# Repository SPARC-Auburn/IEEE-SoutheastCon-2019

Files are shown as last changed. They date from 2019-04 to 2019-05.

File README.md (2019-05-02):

# IEEE Southeastcon Hardware Competition 2019 Team - Auburn University
## Overview
The purpose of this project is to create a robot to compete in the 2019 IEEE SoutheastCon held in Huntsville, AL.  The conference is centered around sharing and demonstrating technical advancements in engineering.  We competed in the hardware competition against 40 other universities from across the southeastern US.  This project was a collaboration between Auburn's [Student Project and Research Committee (SPARC)](http://sparc.eng.auburn.edu/) and an electrical engineering senior design team.

## Game Overview
The function of the robot is to move around a square carpeted area with a side length of 244 centimeters, and pick up small objects on the field and place them into one of four colored home bases based on the color of the object. The arena is split into two zones.  Zone one features four home bases corresponding to four different colors. The robot starts in one of the four home bases.  Zone two is separated by a one-inch thick white line.  Zone two is where twelve objects are placed for the robot to pick up: eight two inch wooden cubes, and four 2.5 inch diameter pit balls. The arena features a wooden box in the middle that serves as an obstacle as well as four LED lights situated at the edge of zone two on the one-inch line.  The four home bases are placed at the four corners of the arena in zone one.  An arena was built in order to test the robot as shown in Figure 0.  This allows testing of the robot in a controlled area leading up to the competition.

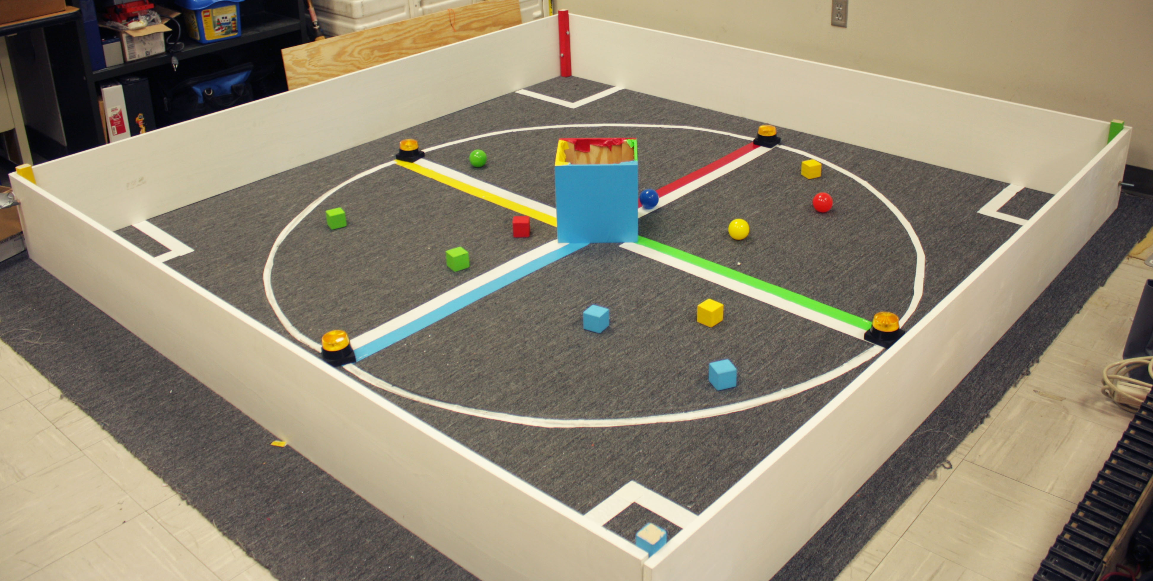
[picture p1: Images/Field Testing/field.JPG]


**Figure 0:** Field Constructed in Broun Hall room 368 

The competition had some other ways to score points such as leaving the home base, going in circles (orbits) around the center structure, and raising a flag.  There is a penalty to colliding with the flashing lights (spacetels).  Table 1 displays a summary of the scoring methods.  

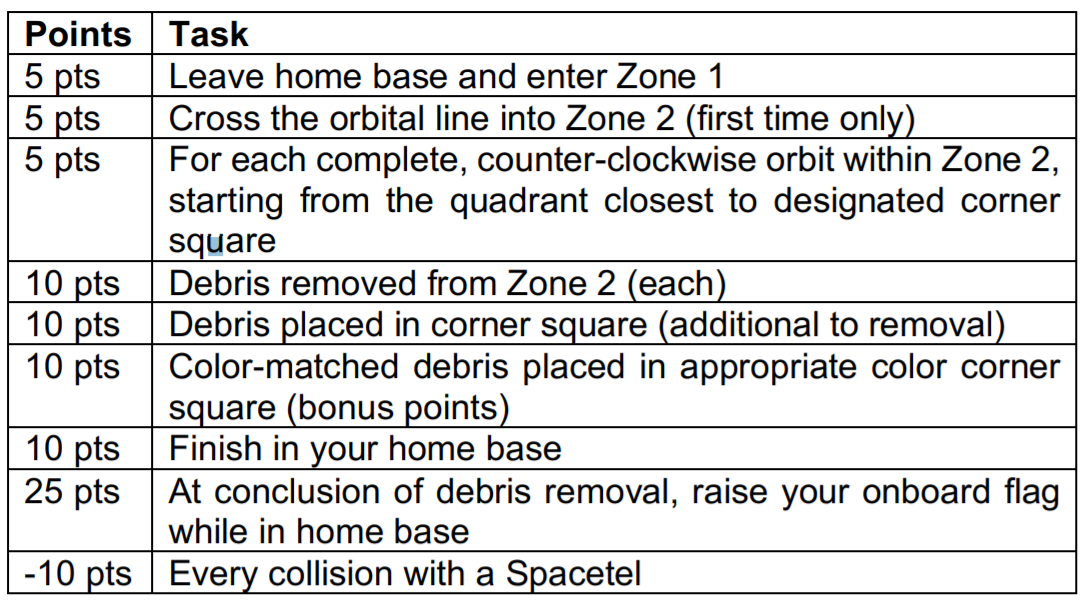
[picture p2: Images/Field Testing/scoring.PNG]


**Table 1:** Summary of scoring methods

## Robot Constraints
The robot has several constraints that limit the size of the robot, materials used in the construction that assure the safety of participants and other robots ([Competition Rules](http://sites.ieee.org/southeastcon2019/files/2019/02/2019-SoutheastCon-HW-Rules_v1_3-1.pdf)).  The robot’s width and length must be within a nine by nine-inch area and a max height of eleven inches.  The nine by nine area must include a bumper covering eighty percent of the perimeter.  The bumper must be 1.5 inches from the ground and have a minimum vertical cover of one inch, and must not have a radius of curvature less than one centimeter.  This is to prevent damage to the arena and other robots in the event of a collision.  The robot can also raise a mechanical arm, with a max length of three inches, with a flag presenting the competing school’s name.

## Our Approach
The robot utilizes two Raspberry Pi microcomputers to control the motors while using an attached camera to identify the color and shape of the objects on the field.  A LIDAR is used to localize the robot on the arena to help avoid the four lights and the wooden box in the middle of the arena.  The design of the robot is to move the objects to the appropriate home base by running over the objects, closing a small door on the front of the robot, hold them under the robot and move towards the appropriate home base of the object.  Figure 1 shows the final robot design.

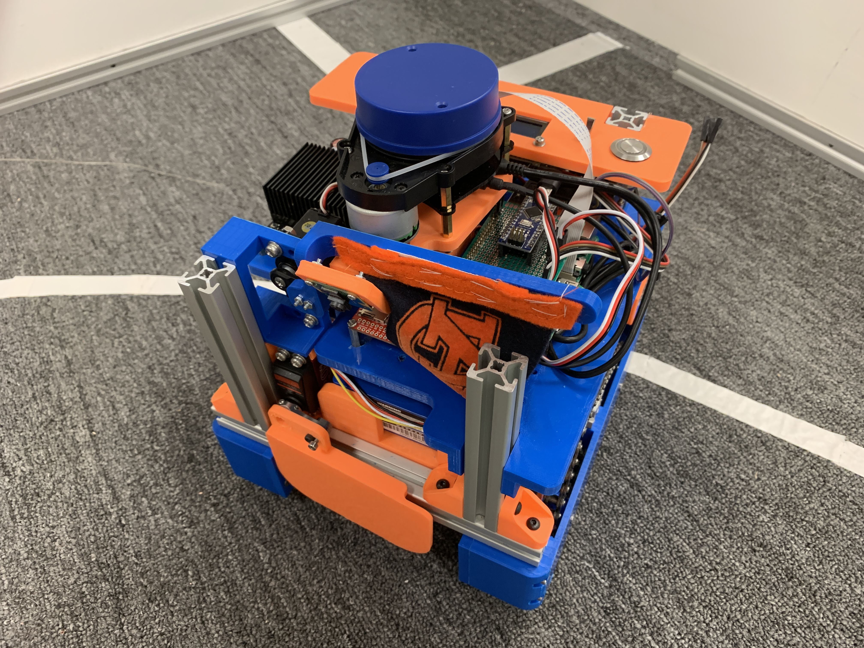
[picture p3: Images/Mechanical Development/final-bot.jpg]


**Figure 1:** Final robot design

## Technical Documentation
* [Mechanical](https://github.com/SPARC-Auburn/IEEE-SoutheastCon-2019/tree/master/Mechanical-Hardware)
* [Electrical Hardware](https://github.com/SPARC-Auburn/IEEE-SoutheastCon-2019/tree/master/Electrical-Hardware)
* [Software](https://github.com/SPARC-Auburn/IEEE-SoutheastCon-2019-Software)

## Team Leadership
* **Team Lead:** Matthew Castleberry (@mcberry23): mtc0030@auburn.edu  
* **Electrical Lead:** Josh Jablonowski (@jdj0019): jdj0019@auburn.edu  
* **Mechanical Lead:** Alex Jones (@alextigernick): naj0016@auburn.edu

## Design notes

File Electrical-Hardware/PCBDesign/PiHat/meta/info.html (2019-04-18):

# RPi B+ Hat

# Raspberry Pi B+ Hat

## Expansion Board

This is a project template for a Raspberry Pi B+ Hat (https://github.com/raspberrypi/hats).

This base project includes a PCB edge defined according to this specification (https://github.com/raspberrypi/hats/blob/master/hat-board-mechanical.pdf). Both a thru-hole and a surface mount connector are provided, along with a different PCB edge for each. Just keep the PCB edge and connector type that you're using for your design and delete the others.

The component footprints used in this template are here (https://github.com/xesscorp/RPi_Hat.pretty).

The board outline looks like this:

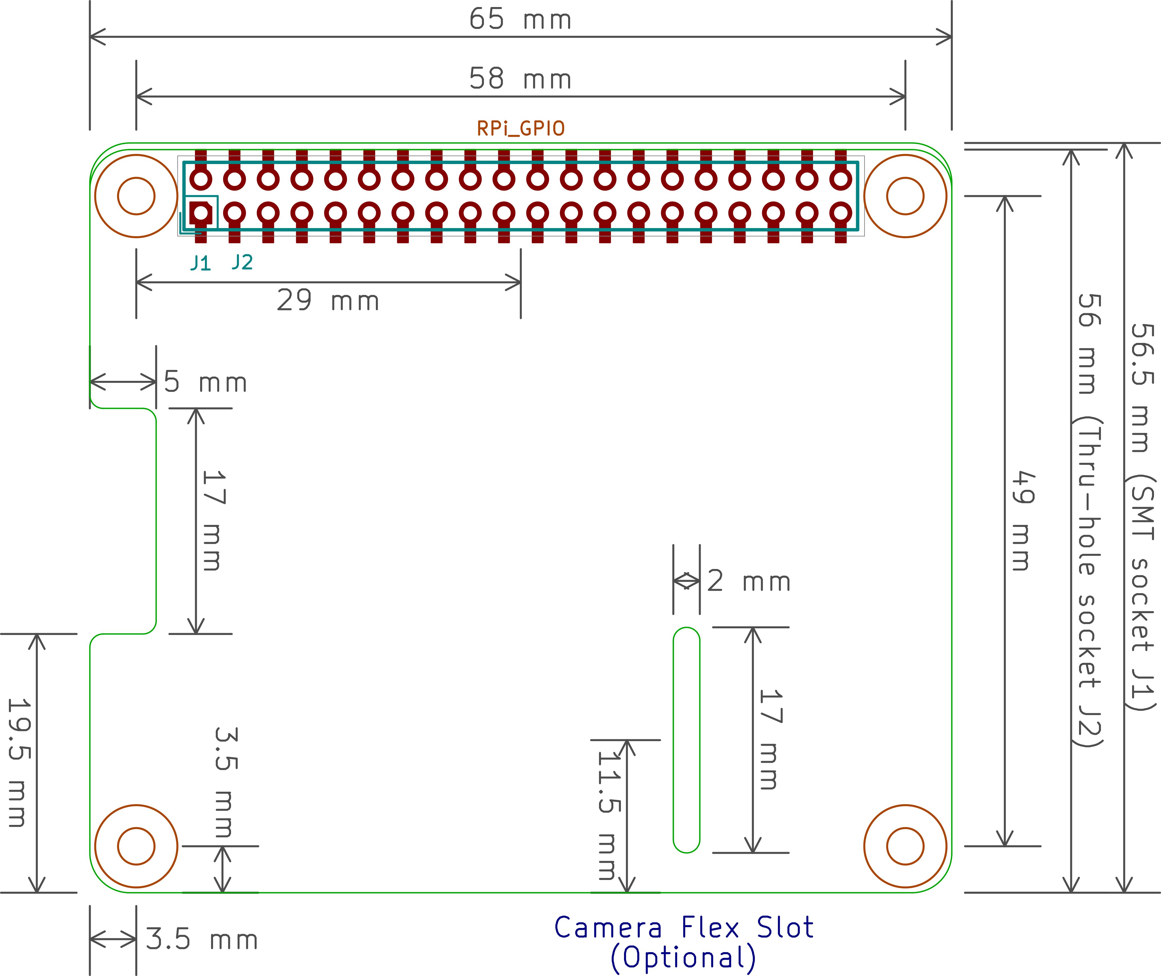
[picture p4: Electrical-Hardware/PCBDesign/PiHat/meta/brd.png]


## Using the Template

To use the Raspberry Pi Hat template with the through-hole connector, do the following:

1. Open the schematic. Remove the SMD connector, J1.
2. Generate the schematic netlist.
3. Generate the .cmp file. (The J2 connector will be the only component in it.)
4. Open the PCB. Hover your mouse over the connector and hit e to edit it. Select the J1 SMD connector. In the Move and Place section of the Footprint Properties window, select the Free radio button. Then click OK. The SMD connector should now be unlocked so it can be removed.
5. Read in the netlist from the schematic. In the Extra Footprints section of the Netlist dialog window, select the Delete radio button. Then click Read Current Netlist. The J1 SMD connector should disappear. Then click Close.
6. Finally, delete the upper two arcs and the edge of the board outline.

To use the Raspberry Pi Hat template with the SMD connector, do the following:

1. Open the schematic. Remove the through-hole connector, J2.
2. Generate the schematic netlist.
3. Generate the .cmp file. (The J1 connector will be the only component in it.)
4. Open the PCB. Hover your mouse over the connector and hit e to edit it. Select the J2 through-hole connector. In the Move and Place section of the Footprint Properties window, select the Free radio button. Then click OK. The through-hole connector should now be unlocked so it can be removed.
5. Read in the netlist from the schematic. In the Extra Footprints section of the Netlist dialog window, select the Delete radio button. Then click Read Current Netlist. The J2 through-hole connector should disappear. Then click Close.
6. Finally, delete the lower two arcs and the edge of the board outline.

(c)2015 XESS Corp.

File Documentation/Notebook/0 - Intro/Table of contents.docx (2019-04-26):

1-Overview

Section 1.1: Abstract

Section 1.2: Project overview

2-Technical documentation

Section 2.1: MECHANICAL Hardware

Subsection 2.1.A: Overview

subsection 2.1.B: Mechanical CAD Drawings

Section 2.2: Electrical Hardware

Subsection 2.2.A: Overview

Subsection 2.2.B: Wiring Diagrams

Section 2.3: Software

Subsection 2.3.A: Overview

Subsection 2.3.B: Using the System

Subsection 2.3.C: Debugging

3- Competition Details

Section 3.1: Post Competition Project Review

Section 3.2: Future work

4- Administrative Documentation

Section 4.1: Budget

Section 4.2: Bill of Materials

Section 4.3: Purchase Orders

Section 4.4: Relationship Between SPARC and Senior Design Proposal

5-Progress Reports

Section 5.1: Project Proposal

Section 5.2: Mid Semester Report

Section 5.3: Final Report

6-Progress Updates

Section 6.1: Fall Meeting Notes

Section 6.2: Spring Weekly Reports

7- Appendices

Appendix A: Datasheets

Appendix B: Source Code

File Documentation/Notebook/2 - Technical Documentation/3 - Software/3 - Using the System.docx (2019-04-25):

Using the System (04/25/19)

The following guide is representative of the system as of the date above. Method of start is likely to change. ALL OF THESE COMMANDS MUST BE RUN IN A LINUX TERMINAL.

The robot is run on ROS, Robotic Operating System. ROS supplies a modular system that does numerous things, but primarily allows different ‘nodes’ to operate on different computers, publishing and subscribing to different topics. In our case, that is two Raspberry Pis. The Pi’s are named d2.local (192.168.1.43) and r2.local (192.168.1.42.). While it is possible to connect to these addresses via VNC viewer, it is recommended to use the ssh command like shown below. You will need two terminal windows for accessing each Pi. (Note: Don’t use the local addresses for connecting to the Pis, use the hostnames d2.local and r2.local)

ssh ubuntu@r2.local

This will allow you to access the terminal for the system without bogging it down, as it is typically sensitive to graphical programs being run on it. Note that both Pis must be connected to the same network to use them independently, and AU_WiFi does not work for that. Using a Wi-Fi hotspot is recommended. If only one is able to be connected, ssh into the other via the first one over its local connection (ethernet).

Now that you are connected, you can begin to run the program. All of the ROS launch files are started via shell files, located in ieee-2019-electrical-software/launches on both Pis.

cd ~/ieee-2019-electrical-software/launches

- To launch the required components for the ROS navigation stack, on d2.local, launch ./ftc.sh.
- To launch AMCL, the move_base node, and the main algorithm node, launch ./amcl.sh on r2.local.

This will boot up the system and begin running whatever is in main_node. If you want to stop the system, it’s recommended to use the kill.py file also located in the /launches file. This way starting new nodes will not overwrite each other and create undesirable bugs.

With the system running, there are several tools ROS provides to allow you to see exactly what is going on in the system. It is recommended to run these on a separate computer or Pi with ROS installed that is connected to the network that the robot is on. This alleviates more computing power from the Pis. To ensure that your ROS computer is getting data from the robot, run the following commands:

cd ~/ieee-2019-electrical-software/

source ros.sh

- rviz – A visual GUI showing the map, current path, current location, and other useful information
  - By default, if the system is connected properly, RViz will boot up with the map server already loaded in from the roscore you connected to with source ros.sh. Allowing you to see what map is currently loaded in
  - To see other topics not listed by default, on the left pane there is a button that says “Add”, which will allow you to add topics to your view panel. In that window, the “By topic” tab will give you the current topics rviz can see that you can subscribe to. (ie. amcl_pose, current robot position)
- rqt_graph
  - Application gives a visual representation of all the nodes the roscore can see and what topics they are publishing and subscribing to.
- rostopic echo topic
  - A simple terminal output of the topic you choose
- rosnode list node
  - Lists the nodes currently running under the roscore

There are numerous commands that ROS also includes that are a bit too in depth to list here, however more information and tutorials on ROS can be found at http://wiki.ros.org/.

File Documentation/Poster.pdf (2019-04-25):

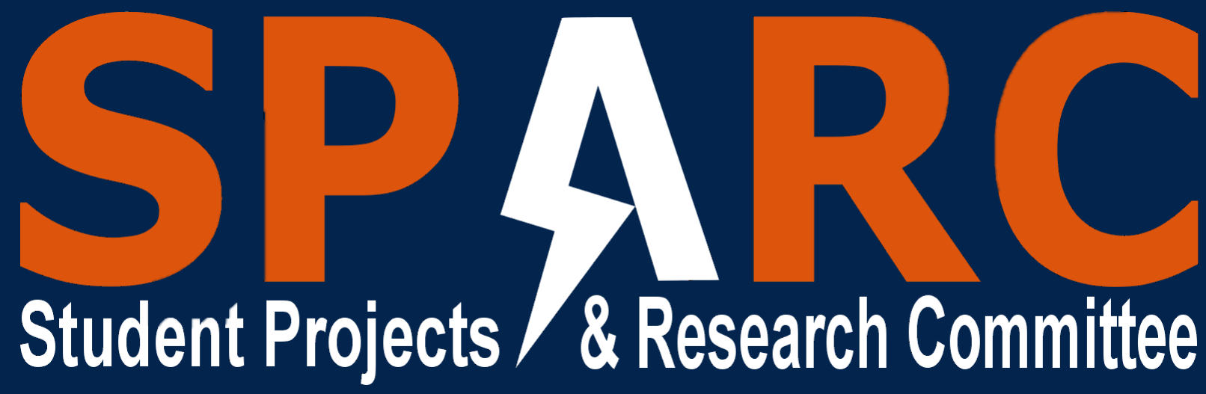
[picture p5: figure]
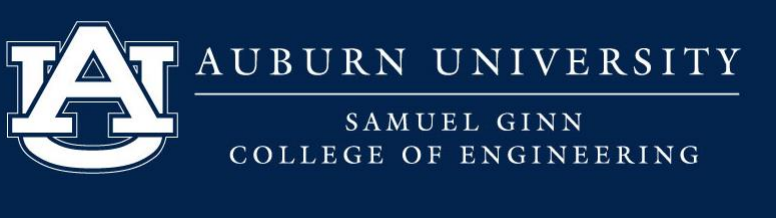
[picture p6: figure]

# IEEE SoutheastCon 2019 Hardware Competition Team

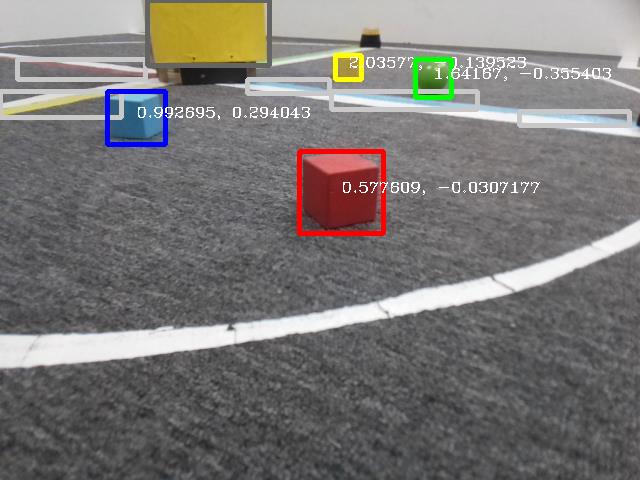
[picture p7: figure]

## Objective

Construct autonomous mobile robot to compete in 3 minute round
Scoring Criteria
5 points for leaving home base
10 points for returning to home base
25 points for raising flag
Up to 15 points per debris move to colored corner 5 points per revolution around center

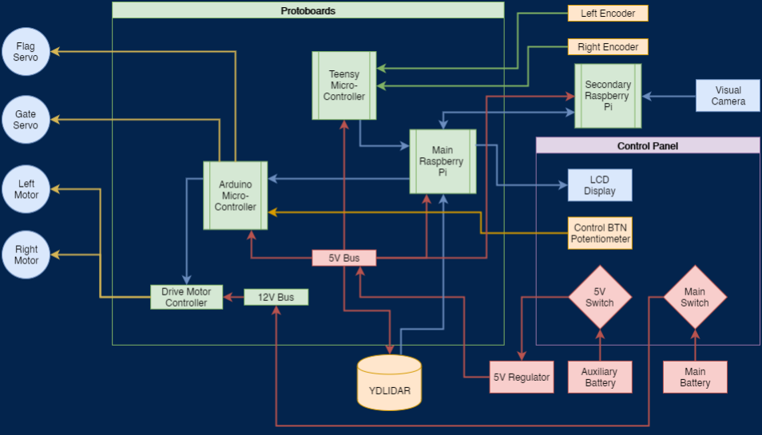
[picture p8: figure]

## Mechanical

## Electrical Hardware

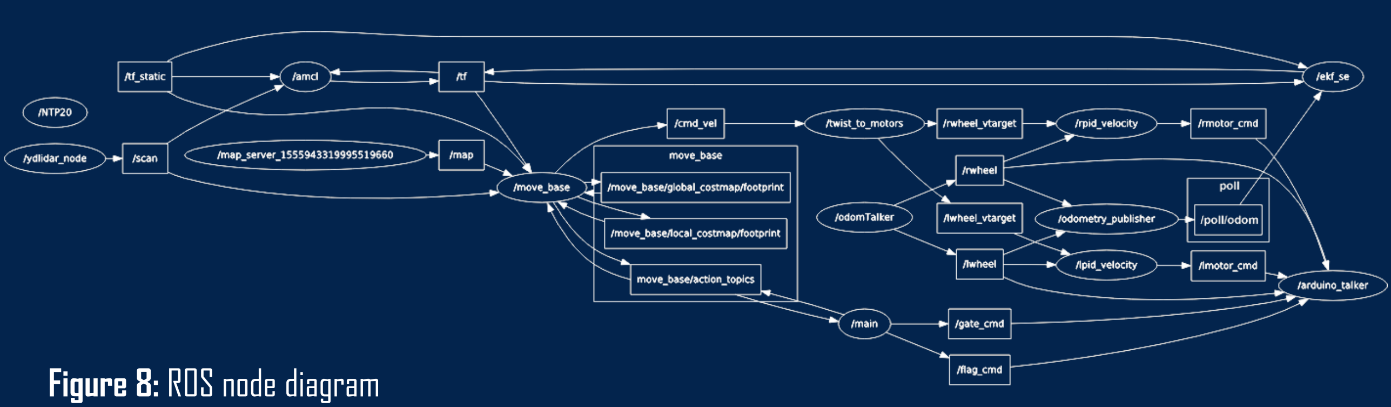
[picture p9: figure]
Figure 8: ROS node diagram

## Localization

## Object Detection

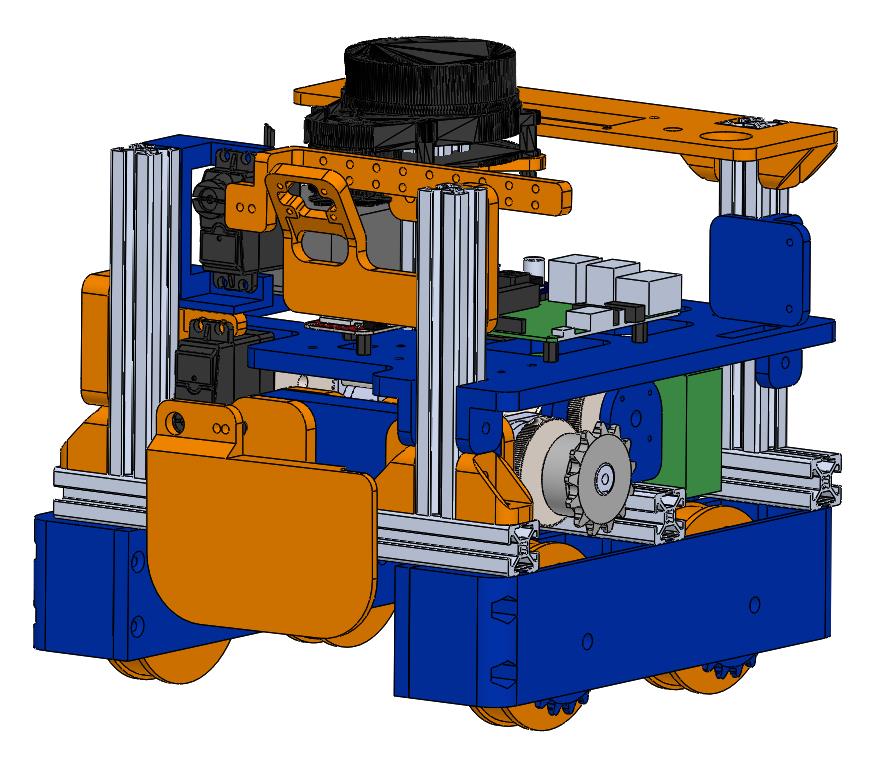
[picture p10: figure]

## ROS

### Senior Design:

## Matthew Castleberry, Joe Hinely, Josh Jablonowski, Nia Perkins

### SPARC:

## William Dovre, Alex Jones, Noah Niedzwiecki, Kevin Ogden, Rebecca Thomas, William Yates

We constructed a 4 wheel differential drive robot. Each side has a motor powering the wheels with a chain and sprocket system. There is an opening with a movable flap in the center section on the bottom for the debris to be collected. The robot fits within the 9” x
9”

x 11” size requirement. It was constructed with an 8020 aluminum frame and custom PLA+ 3D printed brackets.

The robot is controlled using two coprocessing Raspberry Pi 3B+ connected via an ethernet cable. A Teensy microcontroller polls the encoders and sends the velocity information to the main Pi. Once the Pi’s determine a desired path, an Arduino microcontroller instructs the motor controllers of the corresponding commands. Two different batteries are used to prevent the motors from causing a brownout situation for the Raspberry Pi’s.

The LIDAR and encoder data is received on the main Raspberry Pi via USB. Through ROS, this data is processed along with encoder data to determine an x,y position and orientation of the robot with respect to the field. The Adaptive Monte-Carlo Localization (AMCL) algorithm compares the current point cloud to a prerecorded map.

A visual camera image is processed using the computer vision library OpenCV. Through our OpenCV algorithms, the robot can determine an x,y position in meters of each debris object with respect to itself. This is possible because the debris has known sizes that can be compared to the recorded pixel sizes. The algorithm could determine the positions of all 4colors at approximately 10Hz.

Due to the intricate software required to process the selected sensors, we chose the open source framework Robot Operating System (ROS). It consists of a distributed network of nodes. By combining our custom nodes with publicly available nodes, we were able to implement a way to transform the raw collecteddata to commands to control the robot.

While each individual aspect operated nicely when configured properly, the Raspberry Pi’s were not computationally powerful enough to handle the load. ROS and OpenCV are very processing intensive. Adding a second Pi helped distribute the load but increased development time dramatically as well as reduced consistency. In order to properly accomplish the tasks with this approach, a more powerful processor is required such as an Intel NUC.

## Integration

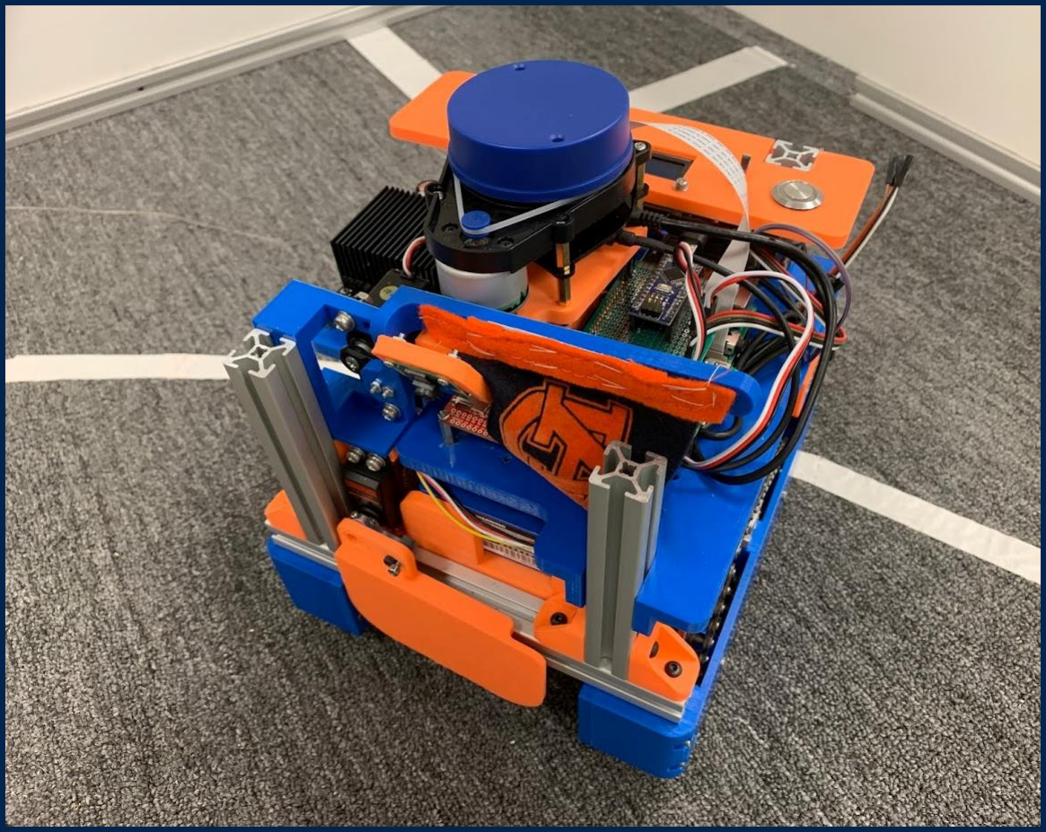
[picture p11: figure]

## Sensors

We selected 3 different sensors to help the robot be aware of its surroundings in the arena: a visual camera, a 2D LIDAR, and rotary encoders. The camera used is the Raspberry Pi Camera Module. The raw images are processed on entirely on a Raspberry Pi to find the debris objects on the field. The LIDAR is a relatively low cost 2D LIDAR system. The YDLIDAR uses a spinning laser rangefinder to return a 2D point cloud at about 8 Hz. The rotary encoders monitor the rotation of each drive motor. The LIDAR and encoders are used for localizing the robot in the field.

Figure 2: Mechanical CAD | Figure 3: Fully assembled platform

Figure 1: Vertical view of playing field

Figure 7: Simplified electrical hardware block diagram

Figure 6: Rotary encoders

Figure 4: Camera module

Figure 5: YDLIDAR

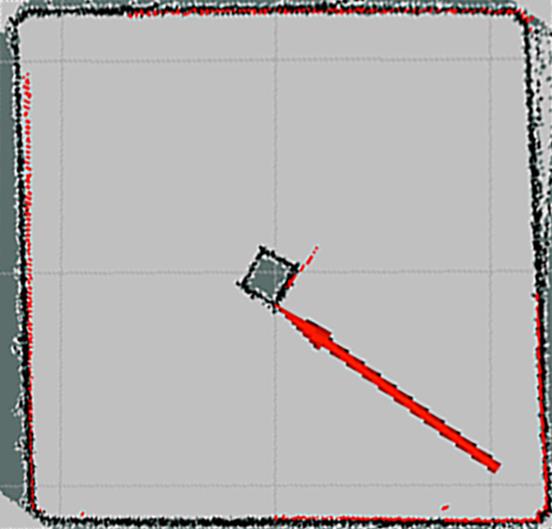
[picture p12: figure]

Figure 9: Robot position and orientation indicated on arena map

Figure 10: Objects identified and analyzed via OpenCV visual processing

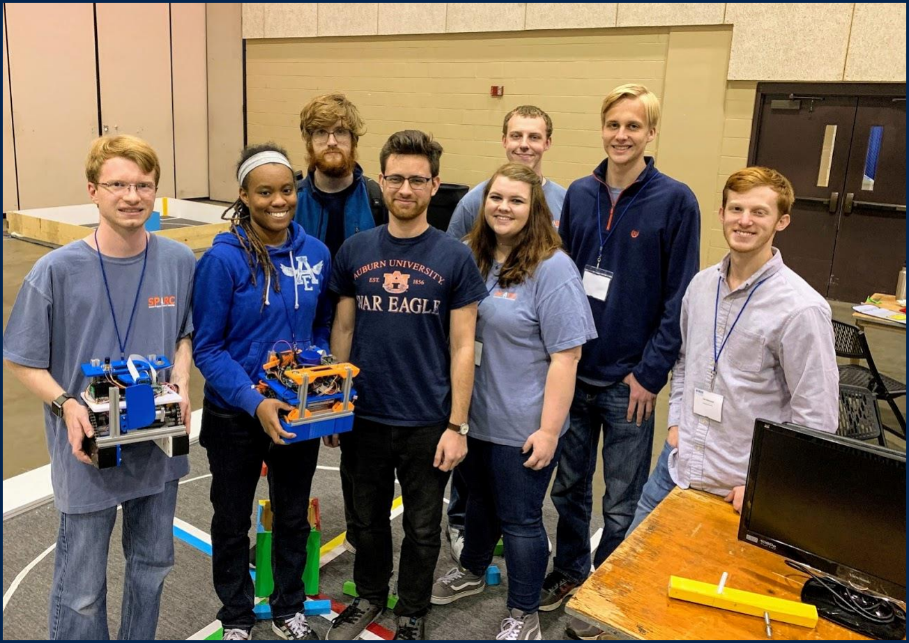
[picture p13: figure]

Figure 13: Full SPARC and senior design team at SoutheastCon 2019 in Huntsville, AL

Figure 12: Field algorithm testing

## Navigation

Once the robot has a coordinate of its current location and its desired location, it can then calculate a path to drive from where it is to where it wants to go. ROS has several different packages that we tried including Dynamic Window Approach, Find the Carrot, and Move Basic. Ultimately Move Basic was the easiest to implement but it is not as smooth as the alternatives.

Figure 11: Example visualization of navigation pathfinding

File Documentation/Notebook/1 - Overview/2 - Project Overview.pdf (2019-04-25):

## Project and Competition Overview

The purpose of this project is to create a robot to compete in the 2019 IEEE SoutheastCon held in Huntsville, AL. The conference is centered around sharing and demonstrating technical advancements in engineering. We competed in the hardware competition against 40 other universities from across the southeastern US.
The function of the robot is to move around a square carpeted area with a side length of 244 centimeters, and pick up small objects on the field and place them into one of four colored home bases based on the color of the object. The arena is split into two zones. Zone one features four home bases corresponding to four different colors. The robot starts in one of the four home bases. Zone two is separated by a one-inch thick white line. Zone two is where twelve objects are placed for the robot to pick up: eight two inch wooden cubes, and four 2.5 inch diameter pit balls. The arena features a wooden box in the middle that serves as an obstacle as well as four LED lights situated at the edge of zone two on the one-inch line. The four home bases are placed at the four corners of the arena in zone one. An arena was built in order to test the robot as shown in Figure 0. This allows testing of the robot in a controlled area leading up to the competition.

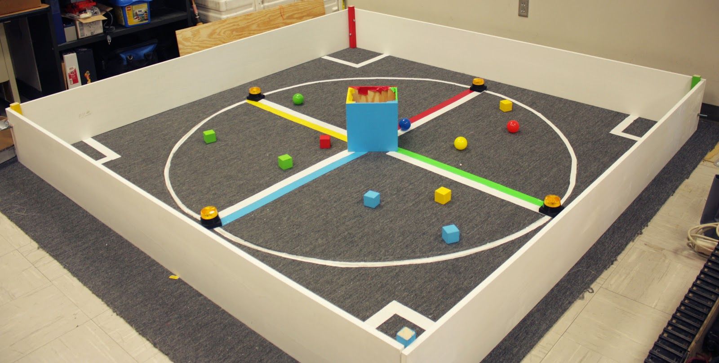
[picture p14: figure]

Figure 0: Field Constructed in Broun Hall room 368 The competition had some other ways to score points such as leaving the home base, going in circles (orbits) around the center structure, and raising a flag. There is a penalty to colliding with the flashing lights (spacetels). Table 1 displays a summary of the scoring methods.

Table 1: Summary of scoring methods [1]

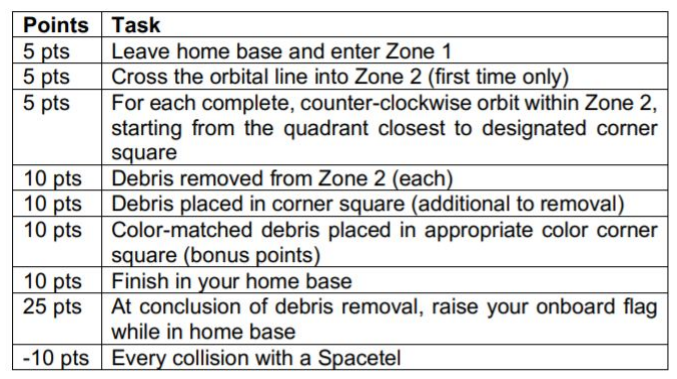
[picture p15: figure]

The robot has several constraints that limit the size of the robot, materials used in the construction that assure the safety of participants and other robots [1]. The robot’s width and length must be within a nine by nine-inch area and a max height of eleven inches. The nine by nine area must include a bumper covering eighty percent of the perimeter. The bumper must be 1.5 inches from the ground and have a minimum vertical cover of one inch, and must not have a radius of curvature less than one centimeter. This is to prevent damage to the arena and other robots in the event of a collision. The robot can also raise a mechanical arm, with a max length of three inches, with a flag presenting the competing school’s name.
The robot utilizes two Raspberry Pi microcomputers to control the motors while using an attached camera to identify the color and shape of the objects on the field. A LIDAR is used to localize the robot on the arena to help avoid the four lights and the wooden box in the middle of the arena. The design of the robot is to move the objects to the appropriate home base by running over the objects, closing a small door on the front of the robot, hold them under the robot and move towards the appropriate home base of the object. Figure 1 shows the final robot design.

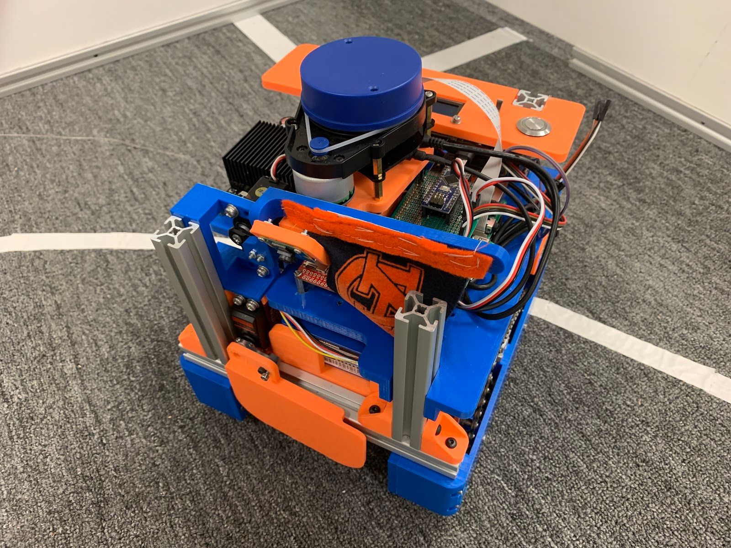
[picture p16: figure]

Figure 1: Final robot design

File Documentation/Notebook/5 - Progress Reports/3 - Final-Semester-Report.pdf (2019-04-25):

# Senior Design Final Report

# IEEE SoutheastCon Hardware Competition

# Auburn University

# April 29, 2019

Matthew Castleberry, Joe Hinely, Josh Jabłonowski, Nia Perkins

## Project and Competition Overview

The purpose of this project is to create a robot to compete in the 2019 IEEE SoutheastCon held in Huntsville, AL. The conference is centered around sharing and demonstrating technical advancements in engineering. We competed in the hardware competition against 40 other universities from across the southeastern US.
The function of the robot is to move around a square carpeted area with a side length of 244 centimeters, and pick up small objects on the field and place them into one of four colored home bases based on the color of the object. The arena is split into two zones. Zone one features four home bases corresponding to four different colors. The robot starts in one of the four home bases. Zone two is separated by a one-inch thick white line. Zone two is where twelve objects are placed for the robot to pick up: eight two inch wooden cubes, and four 2.5 inch diameter pit balls. The arena features a wooden box in the middle that serves as an obstacle as well as four LED lights situated at the edge of zone two on the one-inch line. The four home bases are placed at the four corners of the arena in zone one. An arena was built in order to test the robot as shown in Figure 0. This allows testing of the robot in a controlled area leading up to the competition.


Figure 0: Field Constructed in Broun Hall room 368 The competition had some other ways to score points such as leaving the home base, going in circles (orbits) around the center structure, and raising a flag. There is a penalty to colliding with the flashing lights (spacetels). Table 1 displays a summary of the scoring methods.

Table 1: Summary of scoring methods [1]


The robot has several constraints that limit the size of the robot, materials used in the construction that assure the safety of participants and other robots [1]. The robot’s width and length must be within a nine by nine-inch area and a max height of eleven inches. The nine by nine area must include a bumper covering eighty percent of the perimeter. The bumper must be 1.5 inches from the ground and have a minimum vertical cover of one inch, and must not have a radius of curvature less than one centimeter. This is to prevent damage to the arena and other robots in the event of a collision. The robot can also raise a mechanical arm, with a max length of three inches, with a flag presenting the competing school’s name.
The robot utilizes two Raspberry Pi microcomputers to control the motors while using an attached camera to identify the color and shape of the objects on the field. A LIDAR is used to localize the robot on the arena to help avoid the four lights and the wooden box in the middle of the arena. The design of the robot is to move the objects to the appropriate home base by running over the objects, closing a small door on the front of the robot, hold them under the robot and move towards the appropriate home base of the object. Figure 1 shows the final robot design.


Figure 1: Final robot design

## Technical Overview

### Mechanical Hardware

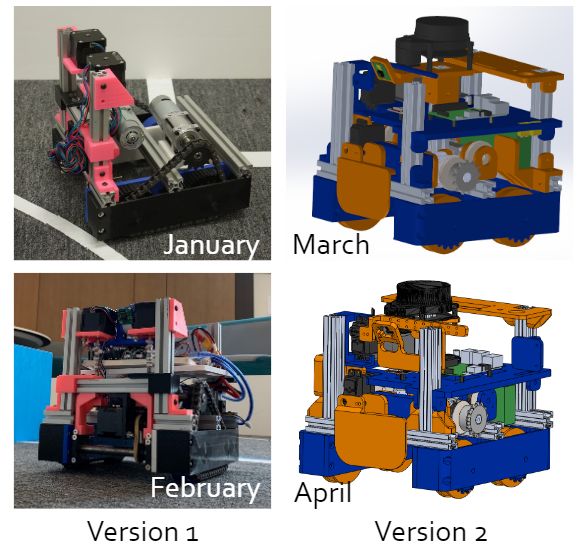
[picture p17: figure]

Figure 2: Mechanical Progression We constructed a 4 wheel differential drive robot. Each side has a motor powering the wheels with a chain and sprocket system. There is an opening with a movable flap in the center section on the bottom for the debris to be collected. The robot fits within the 9” x 9” x 11” size requirement. It was constructed with an 8020 aluminum frame and custom PLA+ 3D printed brackets.

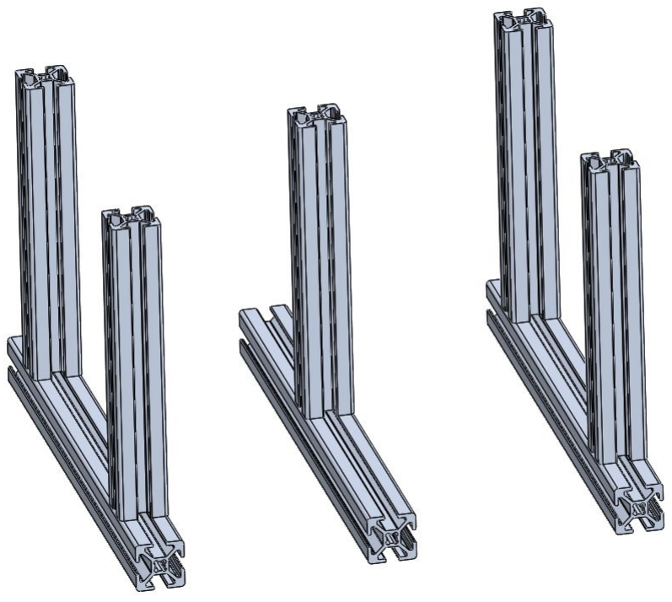
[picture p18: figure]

Figure 3: 8020 Frame
We initially intended on using a spinning rod to actuate vertically to collect and dispose of the debris. We called this mechanism the gate. It utilized three stepper motors. During the testing of the robot, the stepper motors were run using a basic program to make them turn. During this test it was discovered that the rubber tubing connecting the stepper motors to the threaded poles was not tight enough, allowing the motors to slip through the tubing. This, alongside the front gate making the robot front heavy lead to the decision to remove the stepper motors and front gate completely. The front gate can be seen in Figure 2 with the pink 3D printed material and the two servo motors on top. In its place, a servo motor was mounted onto the side of the robot and attached to a paddle that will lift it up to allow objects underneath the robot as shown in Figure 1.
The servo motor not only solves the connection problem of the stepper motors but is considerably easier to program. Removing the added weight from the stepper motors at the top of the gate also lowered the center of gravity. This allows the robot to make more sudden stops and maneuver easier around the obstacles on the field. The simpler mechanical approach helped free up more space for additional electronics.
Another issue that was encountered, was the LIDAR needed to be lowered in order to account for the field being constructed in lumber sizes instead of the state height. At the original position, testing proved that the LIDAR would measure some distances beyond the dimensions of the field. A few different parts of the frame and electronics had to be adjusted to account for this. Once this change was made, the LIDAR could not detect anything above the arena walls.

### Electrical Hardware

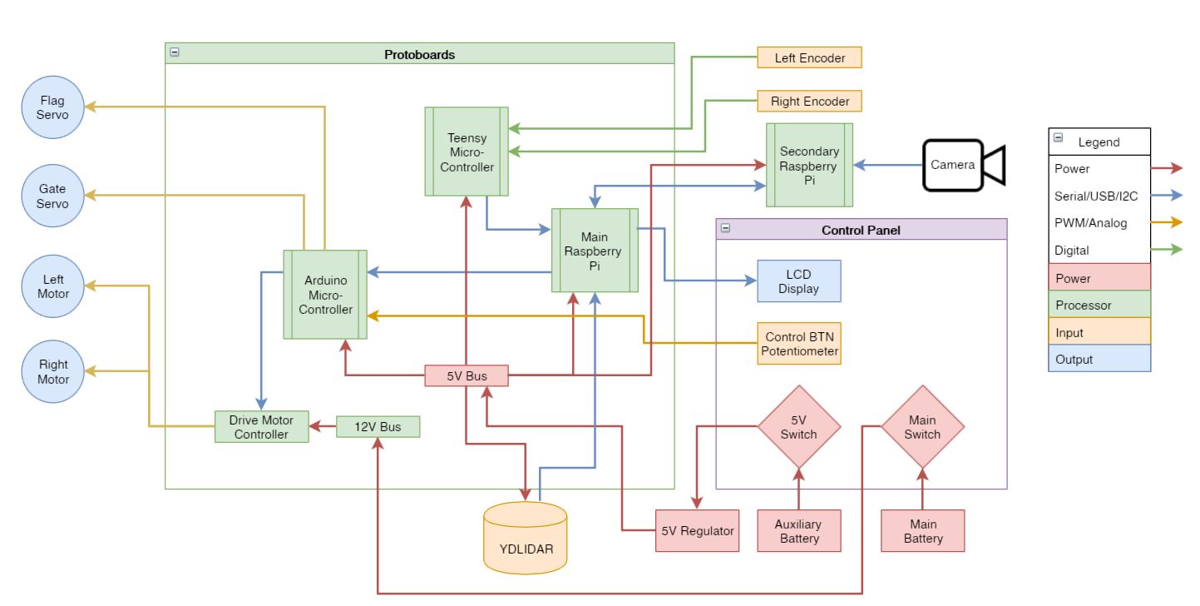
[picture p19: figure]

Figure 4: Electrical Block Diagram We selected 3 different sensors to help the robot be aware of its surroundings in the arena: a visual camera, a 2D LIDAR, and rotary encoders. The camera used is the Raspberry Pi Camera Module. The raw images are processed on entirely on a Raspberry Pi to find the debris objects on the field. The LIDAR is a relatively low-cost 2D LIDAR system. The YDLIDAR uses a spinning laser rangefinder to return a 2D point cloud at about 8 Hz. The rotary encoders monitor the rotation of each drive motor. The LIDAR and encoders are used for localizing the robot in the field. We originally were going to utilize an inertial measurement unit (IMU) to help receive information on orientation and acceleration but we did not use it in the final design.
The robot is controlled using two coprocessing Raspberry Pi 3B+ connected via an ethernet cable. A Teensy microcontroller polls the encoders and sends the velocity information to the main Pi. Once the Pi’s determine the desired path, an Arduino microcontroller instructs the motor controllers of the corresponding commands. Two different batteries are used to prevent the motors from causing a brownout situation for the Raspberry Pi’s. In Figure 4, the latest version of the electrical block diagram shows all of the components on the robot.
To facilitate rapid prototyping, protoboards were used to keep most of the main components centralized to one area and clean up some of the wiring. Two primary peripherals were used to supplement the Raspberry Pi’s as I/O: an Arduino Nano on the main protoboard and a Teensy on its own protoboard. Figure 5 shows a wiring diagram of how the protoboards were utilized.

The Arduino Nano served to wire most of the components together. This includes the servos, buttons, LCD, selector switch, and main motor controller. The decision behind this would be to relieve the processing load from the already over-taxed Raspberry Pi.
The Teensy was required later on in the design process due to the Arduino’s lack of available pins and hardware interrupts to properly implement the encoders. It counts the number of ticks the encoders have counted and sends the values via serial bus to the Raspberry Pi. The Pi can then compute this easily into motor distance traveled.

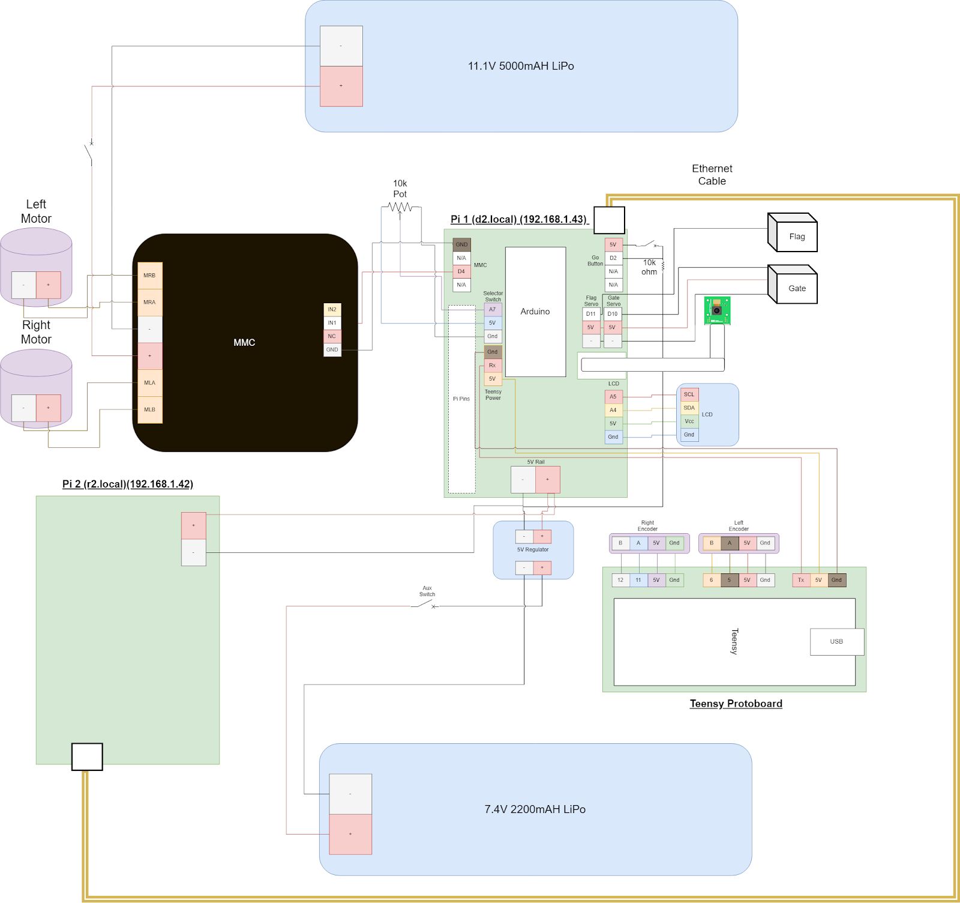
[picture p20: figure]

Figure 5: Wiring Diagram

## Software

### Robot Operating System (ROS)

The need for a simplified approach for localization sparked the switch to using the Robot Operating System (ROS.) ROS greatly simplifies complex localization, mapping, and pathfinding algorithms; all of which are incredibly essential to this competition, although, heed was taken at first because of the vast learning curve coupled with ROS. A very layman's explanation of ROS is that sensor data is input nodes, which house all the vital information for the sensors such as programs, readme files, or launch files. Nodes can talk to each other and request information, process the information, and send to another node. A graphical explanation of how our sensor nodes communicate is shown in Figure 6 below. We have four sensors; LIDAR, Camera, IMU, and encoders that create four ROS nodes. The LIDAR, IMU, and Encoder nodes all input into the localization node, this node coupled with the camera node create what we call the decision maker or essentially a path planner. The decision maker then outputs motor control commands to move the robot.

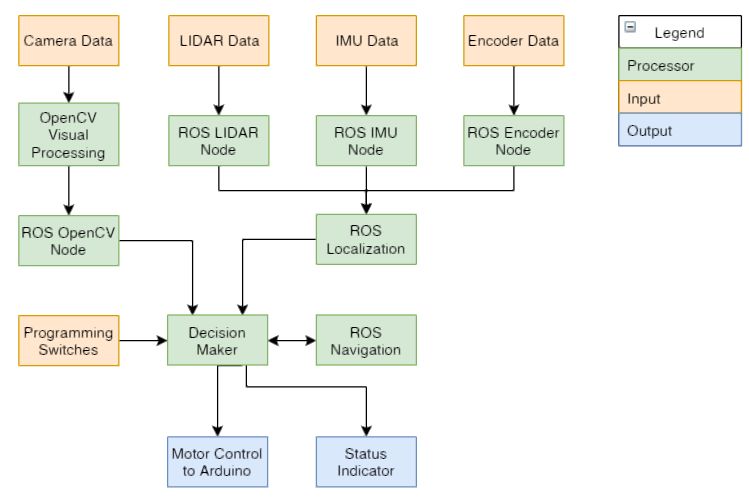
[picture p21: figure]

Figure 6: ROS Node Diagram Figure 7 shows the resulting ROS graph of our implementation. After testing, we determined the IMU was not adding any additional helpful information for localization so it was omitted from the final design.

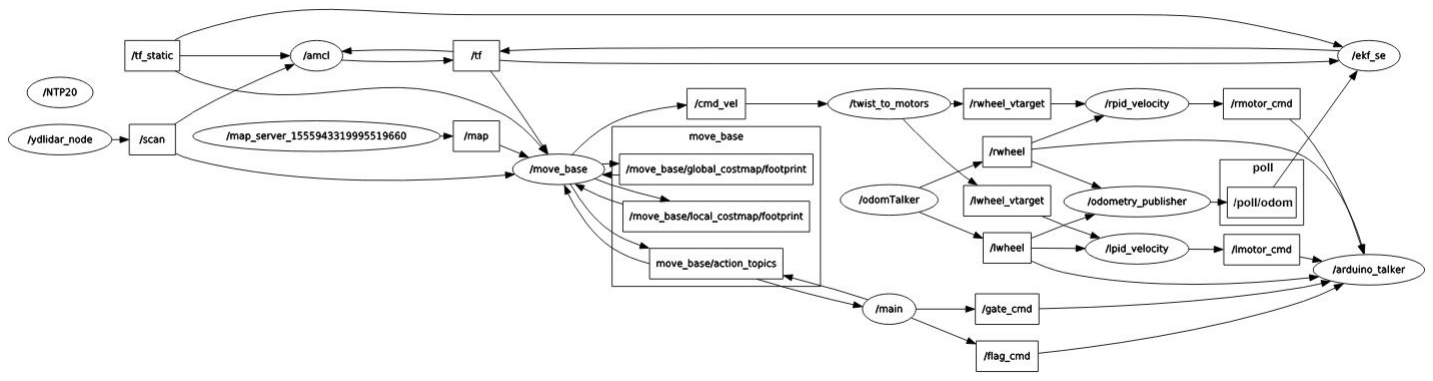
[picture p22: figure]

Figure 7: RQT Graph

### LIDAR and Localization

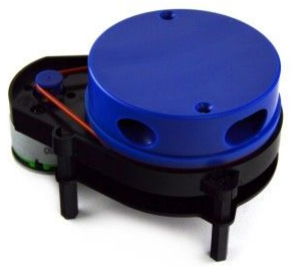
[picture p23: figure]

Figure 8: YDLIDAR
The LIDAR sensor is one of the main components of localization; this sensor acts sort of like a GPS for the robot. The YDLIDAR (Figure 8) has a 360-degree scanning range with a 10-meter range. As stated previously and shown in Figure 7 the LIDAR will be a node, and this is one of two inputs into the localization node. ROS greatly simplifies the localization process as it already has the algorithms needed, one being AMCL. Adaptive Monte Carlo Localization is the process of tracking the pose of a robot against a known map, which is our case. AMCL takes in a map, LIDAR scan, and transform messages, and outputs pose estimates. As stated one of the first things we need to implement the AMCL algorithm is a known map, which is the competition field. Our original process of creating a map was creating a jpeg image and feeding it thru a python program launched within ROS to return a map. However, errors were given when adding the LIDAR scan data to the map. To solve this issue, we had to pre-map the field with actual data using simultaneous location and mapping (SLAM). This proved to be very effective, especially when there was a large skew in the field shape. See Figure 9 for a view of the robot’s orientation and position plotted on a map in ROS.

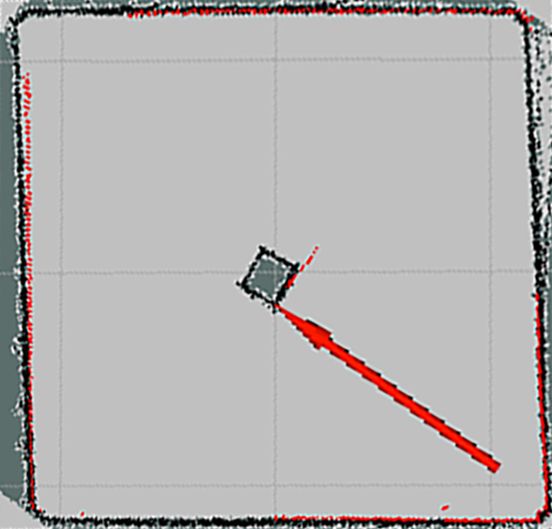
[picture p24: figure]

Figure 9: RVIZ map with localized position and orientation

### Rotary Encoder and Odometry

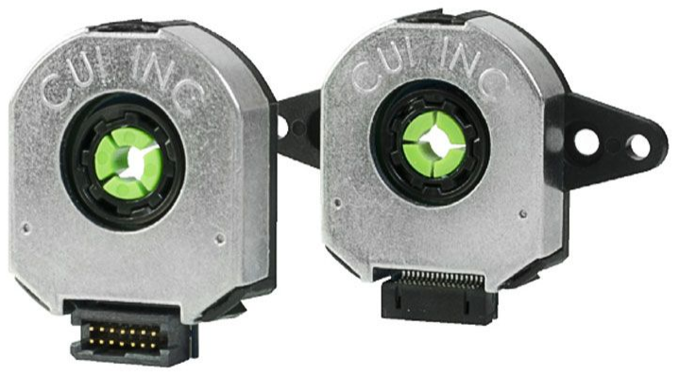
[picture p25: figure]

Figure 10: Quadrature Encoders In order to have more precise measurements in movement, we will use two capacitive encoders attached to the motors. The encoders measure and count the turns of the motors, allowing us to know how far the robot will travel with one motor turn. Using this alongside the localization and object detection, we would be able to move the robot the exact distance towards any detected object to ensure the robot picks up the object. This will also prevent the robot from pushing any object into a position that would make it difficult to pick up.
The encoders are wired and read using a Teensy microcontroller. The Teensy features built in interrupts that allow regular updates from the encoders. This is required as the encoders measure rotations in ticks, these ticks update at a very fast frequency, requiring processing just as quickly. The Teensy reads the encoder ticks and calculates the angular acceleration, which is then sent to the Raspberry Pi via serial.

### Visual Detection

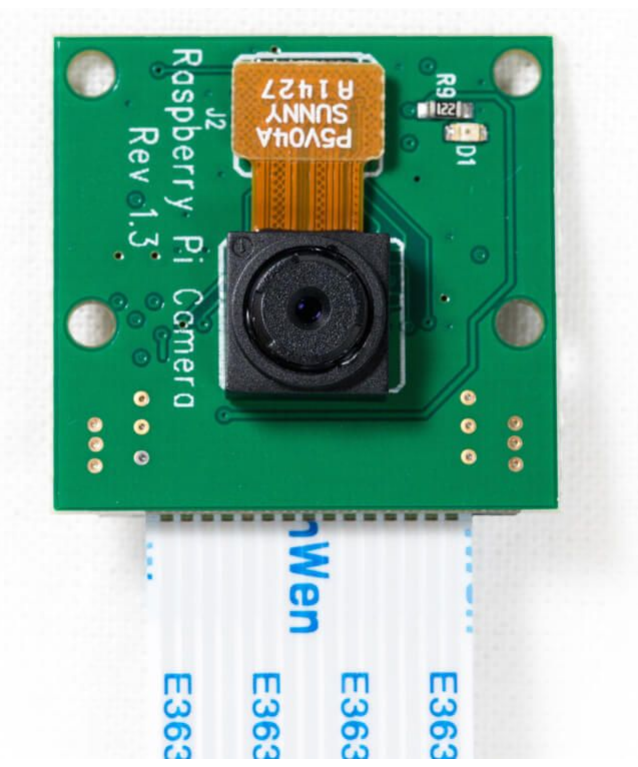
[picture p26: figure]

Figure 11: Raspberry Pi Camera Module We are using the Raspberry Pi Camera Module (Figure 11) to detect the debris objects. By using the open-source computer vision library, the Pi can extrapolate the debris’s pixel location, pixel size, the angle from center, color, type, and approximate distance from the robot. It uses this data to make decisions on where the robot should go. For E-Day, we demonstrated that the robot can turn towards an object, drive until the object is right in front of it and then turn and find a different object. The program worked really well. The biggest issue is that the camera was pointed too far up and needed to be mounted at a lower angle. The next step was integrating visual detection with ROS. A custom message group was created to pass the object information to the main node for navigation.

### Navigation

Once the robot is capable of finding itself on a map with localization, it becomes necessary to plan the steps from point A to point B. There are several ROS nodes available for this that we attempted to use listed below.
- DWA (Dynamic Window Approach)
- Smoother paths
- Requires more computation power
- FTC (Follow the Carrot)
- More simplistic approach, less computation
- Does not avoid obstacles well
- Move_Basic
- Simplest planner
- Turn to goal, move until goal is reached
- Not always accurate
- Does not avoid obstacles
Ultimately, our design settled on Move_Basic, as it provided the simplest approach with parameters that were in our scope of design. Aside from Move_Basic, most path planning algorithms use a form of costmaps. These costmaps determine what path would “cost” the least in terms of time and distance. Most algorithms also use both a local costmap and a global costmap.
The local costmap will calculate where the robot should go in its immediate vicinity, this is usually calculated in real time as the range of the map is shorter and in relation the position of the robot. The global costmap will calculate a path using algorithms such as A* and output something like what is seen in Figure 12. Using both of these costmaps, the robot can efficiently navigate its space avoiding obstacles it can see.

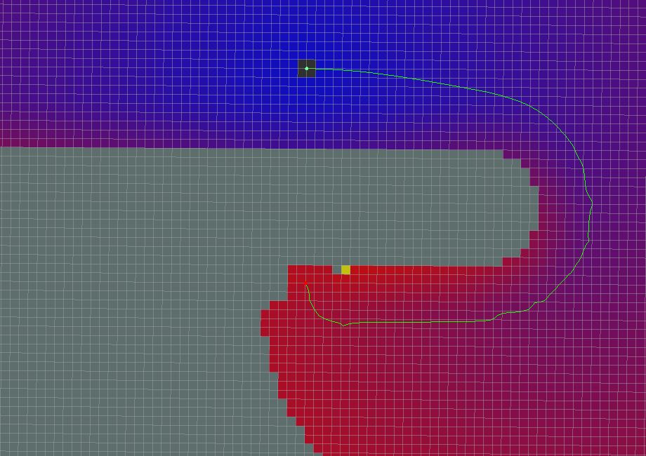
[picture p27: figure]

Figure 12: Example visualization of navigational pathfinding [2]

## Budget

Table 2: Budget Overview

Category | Estimated Cost for 1 Robot | Actual Cost for 1 Robot | Total Expenditures
Electronics (Pi, Sensors, Controllers, etc.) | $170 | $253.63 | $487.26
Electrical Hardware (Batteries, wires, etc.) | $75 | $84.33 | $84.33
Electromechanical (Motors, servos, etc.) | $123.47 | $267.39 | $316.80
Mechanical (Aluminum, 3D printing filament, etc.) | $345.91 | $368.05 | $697.14
Total | $714.38 | $973.4 | $1585.53

## Conclusion

While each individual aspect operated nicely when configured properly, the Raspberry Pi’s were not computationally powerful enough to handle the load. ROS and OpenCV are very processing intensive. Adding a second Pi helped distribute the load but increased development time dramatically as well as reduced consistency. In order to properly accomplish the tasks with this approach, a more powerful processor is required such as an Intel NUC.
Our robot was the most complex from an electrical and software perspective at the competition. Despite the lack of success at the competition, we learned a lot. Most of the key aspects of the robot worked very well just not simultaneously. An improvement in hardware could dramatically improve performance.

## References

[1] “2019 SoutheastCon Hardware Rules v1.3.” IEEE, Huntsville, 18-Aug-2018. “http://sites.ieee.org/southeastcon2019/files/2019/02/2019-SoutheastCon-HW-Rules_v1_3-1.pdf ”
[2] “ROS Global Path Planner.” ROS, 24-Apr-2019. “http://wiki.ros.org/global_planner”

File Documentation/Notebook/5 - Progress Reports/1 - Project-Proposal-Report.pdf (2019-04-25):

# Senior Design Project Proposal

# IEEE SoutheastCon Hardware Competition

# Auburn University

# January 21, 2019

Matthew Castleberry, Joe Hinely, Josh Jabłonowski, Nia Perkins

## Project Overview

The purpose of this project is to create a robot to compete in the 2019 IEEE
SoutheastCon held in Huntsville, AL. The purpose of the conference is to share and demonstrate technical advancements in engineering. We will be competing in the hardware competition against other universities from across the southeastern US.
The purpose of the robot is to move around a square carpeted area with a side length of 244 centimeters, and pick up small objects on the field and place them into one of four colored home bases based on the color of the object. The arena will be split into two zones. Zone one features four home bases corresponding to four different colors. The robot will start in one of the four home bases. Zone two is separated by a one inch thick white line. Zone two is where twelve objects will be placed for the robot to pick up: eight two inch wooden cubes, and four 2.5 inch diameter pit balls. The arena will feature a wooden box in the middle that will serve as an obstacle as well as four LED lights situated at the edge of zone two on the one inch line. The four home bases will be placed at the four corners of the arena in zone one. An arena was built in order to test the robot as shown in Figure 1. This allows testing of the robot in a controlled area leading up to the competition.
The robot has several constraints that limit the size of the robot, materials used in the construction that assure the safety of participants and other robots [1]. The robot’s width and length must be within a nine by nine inch area, and a max height of eleven inches. The nine by nine area must include a bumper covering eighty percent of the perimeter. The bumper must be 1.5 inches from the ground and have a minimum vertical cover of one inch, and must not have a radius of curvature less than one centimeter. This is to prevent damage to the arena and other robots in the event of a collision. The robot can also raise a mechanical arm, with a max length of three inches, with a flag presenting the competing school’s name.
The robot utilizes a Raspberry Pi chip to control the motors of the robot, while using an attached camera to identify the color and shape of the objects on the field. A LIDAR will be used to localize the robot on the arena to help avoid the four lights and the wooden box in the middle of the arena. The robot will move the objects to the appropriate home base by running over the objects, closing a small door on the front of the robot so the robot can go backwards without losing any objects, hold them under the robot and move towards the appropriate home base of the object.


Figure 1: Field Constructed in Broun Hall room 368

## Management Approach

This project was initiated by Auburn University’s Student Projects and Research Committee (SPARC) at the end of Spring 2018 semester. The team is split into two sub-teams: mechanical and electrical. The mechanical team is responsible for the design and constructing the robot’s mechanical system focusing on the frame, mobility system, debris collection system, and flag raiser. The electrical team is responsible for selecting and wiring the electrical hardware components as well as writing the software to make them operate as desired. In order to increase the amount of effort put into the project, this senior design team has been formed to be a part of the electrical sub-team.
One of SPARC’s primary functions is to display the status of its projects at E-Day during late February each year. Because this project is considered a major SPARC project, it is desired that it be in a minimally operational state by February 22, 2019. The goal is the robot would be able to autonomously push debris into the corresponding corner. After this deadline, the remaining work will be focused on tuning and diversifying the algorithm as well as accounting for an opponent robot.
Based on the previous development and this semester’s two-phase development plan, this project most closely corresponds with the agile methodology. The tasks will be grouped into sprints in which each “has a defined duration (usually in weeks) with a running list of deliverables, planned at the start of the sprint” [2]. The project has multiple components that must be developed separately and then later integrated thus the first half of a sprint will be component focused and the second half will be focused on integration.

## Technical Approach

### Mechanical Strategy

The robot had three initial designs, a conveyor belt, a forklift to pick up the object, or pushing the object around. Each design worked on the basis of the robot running over the objects, however the conveyor belt and forklift used a tank to hold the objects in after lifting them. The conveyor belt design involved moving over the object and lifting them into a tank on the robot using notches on the belt to catch the objects. The forklift featured foam fingers located under the robot that picked up objects, lifted them through the robot and placed them into the tank. The final design removed the tank on the back of the robot, instead holding the objects under the robot while moving.


Figure 2: Current Status of Mechanical Platform In order to keep the objects under the robot while moving backwards, the robot will have a 3D printed gate that is moved up and down using two small motors. The 3D printed sections can be identified by the pink and blue sections of the test robot, with the black motors on the front of the robot controlling the gate shown in Figure 2. The gate is raised to gather objects and closed to hold the objects under the robot until it reaches the appropriate home base. The front of the robot will also use a pole covered in flex seal that turns in order to pull objects under the robot.
For easy modification and building, the wheels and connections of the robot are 3D printed, the wheels forever have little to no traction, this is fixed by covering the wheels in flex seal in order to create traction against the carpet arena. The robot has two main motors. Due to availability, the robot uses two 70 Amp motors to drive the wheels and two motor controllers for the smaller motors controlling the front gate.

### Electrical

Because this is an autonomous competition, our robot must be able to identify colors, locate them on the field, figure out the distance between the debris, other debris and how far it is away from its drop location while also recognizing where its current position is in the field to avoid spacetels and the centerpiece. Our approach to being able to identify space debris is with a camera mounted on the robot. OpenCV is used to program a debris recognition algorithm which is explained more in the software section. The camera selection was between a single camera or a stereo camera. The stereo camera is a two camera setup that gives vision more similar to human eyesight. This would be nice however this would require more processing power than our raspberry pi can handle. The single camera focuses on color instead of depth which is what we need, so the single was the better choice.
For the robot to be able to tell where its location is with respect to the playing field we need a device. The electrical team tackled with two approaches LIDAR vs. four distance sensors. The four sensors seem like a better approach, but actually, it requires a more complex algorithm since you have four different points to process. With the four sensors you have four data points to determine the robotics location on the field, which depending on the robotics location it may not be able to give an accurate location with the four sensors. The LIDAR however gives you a location with multiple data points which allows for a more precise location.The LIDAR does give more data but this allows for a more precise location.
Lastly, we had to decide rather use one battery or two. From you the pugh chart in Table 1, the two batteries is a better choice. This allows us to use a larger battery for the motors and smaller battery for the Pi. This prevents from brownout during a round.
Table 1: Pugh chart for number of batteries
Criteria | Weight | One | Two
Safety | 2 | -- | +++
Reliability | 2 | -- | ++
Cost | 1 | + | -
Robot space | 1 | ++ | -
+ | 3 | 5
0 | 0 | 0


- | 4 | 3
Total | -1 | 3

Figure 4: Electrical Block Diagram Figure 4 shows a block diagram of the proposed electrical system. It is comparing two different configurations of controlling the motors. Currently on the test platform shown in Figure 5, the motor controllers require pulse width modulation (PWM) signal. Because the Raspberry Pi does not support multi-channel PWM, an Arduino microcontroller is used to supply the PWM. If new motor controllers with serial support are purchased, the Arduino can be eliminated therefore simplifying the design.

Figure 5: Electrical Test Platform

### Software

Programming Language Selection
One of the first major decisions the team had to make for software development was which programming language we were going to use. We compared the two most popular programming languages for robotic applications, Python and C++. Both had support for the selected visual processing library, OpenCV. After considering the ease of development and online support of python versus the stability and processing speed of C++, we determined that C++ was the better option. See Table 2 for a pugh chart comparing the two languages.
Table 2: Pugh Chart for Programming Languages
Criteria | Weight | Python | C++
Ease of development | 1 | ++ | -
Stability | 2 | - | ++
Online Support | 1 | +++ | +
Processing Speed | 2 | - | ++
Available Libraries | 1 | ++ | +
+ | 7 | 10
0 | 0 | 0
- | 4 | 1
Total | 3 | 9

Debris Detection Via Visual Processing
In order to detect the debris objects, a visual camera is placed on the front of the robot. The powerful open source C++ computer vision library, OpenCV, is utilized to interpret the images the camera receives. The program analyzes the colors in the picture by creating four pictures of a black background with white indicating the pixels of the corresponding color (Figure 6). OpenCV’s contour detection function is then used to find all of the edges. A bounding box and circle are placed around each of the contours. By comparing the size of the bounding box and circles, the shape and approximate pixel size of the objects can be determined.


Figure 7 shows the resulting image by running the program on a static image. The corresponding data returned is listed in Figure 8.

Figure 6: Color Filtered Analysis of Debris, red (top left), yellow (top right), green (bottom left), blue (bottom right)

Figure 7: Demonstration of Debris Detection Program on Static Image

1. Red blck | @ [855, 1296] | -34.3 degrees | w/ width 211 | and height 200
2. Red ball | @ [2029, 1201] 44.6 degrees | w/ radius 102
3. Red blck | @ [810.5, 1082] -29.4 degrees | w/ width 110 | and height 84
4. Blue blck | @ [1784, 1592] 54.2 degrees | w/ width 316 | and height 372
5. Blue blck | @ [713, 1120] | -35.3 degrees | w/ width 133 | and height 109
6. Yellow ball @ [1216, 1186] -6 degrees | w/ radius 91
7. Yellow blck @ [1380, 1102] 5.66 degrees | w/ width 111 | and height 108
8. Green ball | @ [1462, 1051] 10.5 degrees | w/ radius 51.1
Figure 8: Output from Debris Detection Program The remaining work to be accomplished is to determine the distance the objects are from the camera. There is an example python program accomplishing this by calibrating the camera to a known object [3]. Since the blocks and balls are known, definite sizes, this method should be fairly reliable. The entire visual detection program also has to be integrated other software in order to provide all of the functionality required for an operational robot.
LIDAR Analysis


Figure 9: Image of YDLIDAR In order for the robot to know where it is on the playing field, we are using a LIDAR. A LIDAR sensor uses a spinning optical sensor to measure the distance to nearby objects very similar to how a RADAR sensor works. During the fall semester, a low-end 2D LIDAR sensor, the YDLIDAR, was purchased as shown in Figure 9. From work done last semester, a program was developed to record all of the points measured in a single rotation of the sensor. The results are displayed in Figure 10.


Figure 10: Plot of Detected Points from LIDAR Another program was developed to approximate the x,y coordinate of the location of the sensor with respect to the walls. It uses a technique called rotating calipers to fit a square around the field as shown in Figure 11. From this information, we can program where the robot can and cannot go based on the current location. Further testing needs to be done to prove the program works in all cases especially as the robot approaches the center structure. If the program works accurately, then it will need to be integrated into rest of the functionality of the robot.


Figure 11: Analysis of LIDAR Data

Utilization of Robot Operating System (ROS)
A popular robotics C++ library, Robot Operating System (ROS), exists to ease the integration of various sensors and devices on robots. Much discussion has taken place on whether or not this library would be helpful. The benefits are it may have many algorithms and tools built in to help make sense of the data received from the sensors. The downside is that it is most commonly used on systems with communication back to an external computer and the learning curve is fairly steep. The alternative is a custom integration of the individual software components. At this point in time, it does not look beneficial to utilize ROS but it will be reconsidered at a later point if needed.

### Integration

Since there are many significant parts to the robot with many design decisions, it is important to consider what challenges may take place in integrating major parts.
The mechanical and electrical teams must integrate their parts to ensure electronics have space to sit on the finished robot. Motor controllers must be selected to match the requirements of the motors selected by the mechanical team. The battery that is selected must also be able to support the motors and other mechanical systems on the robot.
Electrical and software integrations must also take place for the systems to communicate properly. After a decision has been made on what type of communication the motor controllers will require- serial or PWM- appropriate wires must be terminated at the Arduino and Raspberry Pi. These connections must also be made to the motor controllers.
Since the software is divided into two major components, object detection and LIDAR localization, there will need to be software written to fuse the information appropriately. This will happen a few weeks before each development cycle. In addition to sensor development, an efficient algorithm will need to be developed based on the inputs received by the software.

## Budget

The chart in Table 3 includes an expected Bill of Material (BOM) of the parts that will be needed for this project, separated by the portion of the robot they are for. i.e. mechanical, electrical, software. All funding for parts will come through SPARC, approved by Dr. Roppel. Some parts have already been purchased, and are marked accordingly. Note that the components used for the arena are not included in this BOM.
Table 3: Predicted Budget

MECHANICAL
Part | Quantity | Price/per | Total | Ordered?

2020 Extrusion | 96in | $0.16 | $17.32 | Y
2020 nuts m4 | 50 | $0.21 | $10.50 | Y
100x M4 Button Screws | 1 | $9.90 | $9.90 | Y
Flanged Bearings | 8 | $3.97 | $31.76 | Y
Shaft Collars | 8 | $3.89 | $31.12 | Y
12" Shaft | 1 | $7.72 | $7.72 | Y
6-32 Thread Size, 1-1/4" Long, wheel screws | 1 | $6.80 | $6.80 | Y
6-32 Thread Size,wheel/frame nuts | 1 | $3.40 | $3.40 | Y
6-32 Thread Size, 2" Long, frame screws | 1 | $6.90 | $6.90 | Y
Intake Rod | 1 ft | $5.45 | $5.45 | Y
NEMA Screws | 1 | $4.18 | $4.18 | Y
Hex Nuts | 2 | $2.14 | $4.28 | Y
Lead Screws | 1 | $5.14 | $5.14 | Y
Lead Screw Coupling Tubing | 10ft | $7.00 | $7.00 | Y
50x 10-32 Screws | 1 | $6.06 | $6.06 | Y
motor sprockets | 2 | $13.85 | $27.70 | Y
Motors | 2 | $7.25 | $14.50 | Y
Gearboxes | 2 | $56.50 | $113.00 | Y
Gearbox Mount Accessories | 2 | $4.50 | $9.00 | Y
Chain | 1 | $16.88 | $16.88 | Y
Chain Tools | 1 | $21.80 | $21.80 | Y
NEMA 17 Vertical Bar Actuator | 3 | $12.99 | $38.97 | Y
MECHANICAL TOTAL BUDGET | | | $399.38
ELECTRICAL
Raspberry Pi 3B+ | 1 | $30.00 | $30.00 | Y
Arduino Uno | 1 | $20.00 | $20.00 | Y
3 Stepper Motor Driver | 1 | $30.00 | $30.00 | N
Dual DC Motor Driver (70A inrush) | 1 | $30.00 | $30.00 | N
Auxillary LiPo Battery | 1 | $30.00 | $30.00 | N
Main 12V LiPo Battery | 1 | $30.00 | $30.00 | N
5V Voltage Regulator | 1 | $10.00 | $10.00 | N
Raspberry Pi Camera V2.1 | 1 | $20.00 | $20.00 | Y
Raspberry Pi Camera Ribbon Cable | 1 | $10.00 | $10.00 | N
USB-B to USB-A Cable | 1 | $5.00 | $5.00 | Y

YDLIDAR Module | 1 | $100.00 | $100.00 | Y
Various Connectors and Wires | 1 | $0.00 | $0.00 | Y
ELECTRICAL TOTAL BUDGET | | | $315.00
FULL ESTIMATED PROJECT BUDGET | | | $714.38

## Major Roles

Due to the challenge of managing a large team, this project will require major roles to be divided evenly amongst the team members. The distribution is shown below in the organization chart in Figure 12. Note that the members of the senior design team are in yellow, and are all a part of the electrical team. The primary focuses of the senior design team will be electrical hardware, LIDAR localization, computer vision algorithms, navigation algorithms, and overall team management.


Figure 12: Organizational Chart

## Timeline

Table 4 lists the weekly tasks for each aspect of the team. Figure 13 summarizes the table in the form of a Gantt chart. The project is split into three different cycles. The first cycle is to create a minimally operational robot that can move debris into the corresponding corner. This milestone is set to be completed for a demonstration at E-day on February 22nd. The second cycle is to finish the design, test alternative algorithms, and construct a second robot. A second robot will be useful in testing so that we can test the program for the final rounds. It also is a good backup to have two full robots for the competition in case of part failure. The third phase will take place after the competition and will be focused on preparing for the final presentation.
Table 4: Weekly Tasks to be Accomplished
Week | General | Mechanical | Electrical | Senior Design
Jan 7-11 | Team Leads meet to discuss current progress, immediate actions, and competition | Continue Assembling prototype #1 | Test serial control and vision detection program developed last semester | Form Team
Jan 14-18 | First general SPARC meeting of the semester | Cont. | Tune full program, develop LIDAR program | Develop project proposal
Jan 21-25 | | Cont. | Cont. | Keep up with required documentation
Jan 28-1 | | Prototype #1 mobility system completed, start integrating electronics | Start integration on hardware
Feb 4-8 | | Improve prototype #1 | Further tuning and integration
Feb 11-15 | | Cont. | Cont.
Feb 18-22 | E-Day Demonstration: Prototype #1 can put debris in the correct corner
Feb 25-1 | Travel Team Applications are released | Design prototype #2 | Develop alternative programs,
Mar 4-8 | | Start assembling prototype #2 | Cont.
(Spring Break) Mar 11-15 | Deadline for travel team applications (Mar 11), Register for conference and hotel
Mar 18-22 | | Test both robots on field | Test both robots on field
Mar 25-29 | | Cont. | Cont.
April 1-5 | | Cont. and 3D print extra parts | Cont.
April 8-12 | Week of Competition

April 15-19 | Cleanup and organize labs | Cleanup and organize labs | Prepare poster, practice demonstration
April 22-26 | | | Senior Design Fair


Figure 13: Gantt Chart of Project Timeline

## Facilities to be Used

This project will utilize two labs located in Broun Hall 367 and 368. Both labs are supervised by Dr. Roppel. Broun 367, the SPARC lab, will be used for design and prototyping. Broun 368 will be used as a test area, housing the 9`×9’ test arena. All hardware will be stored in these two labs on campus for the duration of the project.

## Conclusion

Overall, we are constructing a robot to autonomously move small blocks and balls into coordinated colored corners. The technical deadline for this project is April 10th with a major operational milestone of February 22nd. The operating technical budget is $714.38.

## References

[1] “2019 SoutheastCon Hardware Rules v1.2.” IEEE, Huntsville, 18-Aug-2018. “http://sites.ieee.org/southeastcon2019/files/2018/09/2019-SoutheastCon-HW-Rules_v1_2.pdf”
[2] “Waterfall vs. Agile: Which Methodology is Right for Your Project?,” Segue Technologies, 20-Nov-2018. [Online]. Available: https://www.seguetech.com/waterfall-vs-agile-methodology/. [Accessed: 16-Jan-2019].
[3] “Find distance from camera to object using Python and OpenCV,” PyImageSearch, 05-Dec-2018. [Online]. Available: https://www.pyimagesearch.com/2015/01/19/find-distance-camera-objectmarker-using-python-opencv/. [Accessed: 16-Jan-2019].
[4] Jarema, R., & Jarema, R. (2018, April 12). Batteries - choose the right power source for your robot. [Online]. Available: https://medium.com/husarion-blog/batteries-choose-the-right-power-source-for-your-robot-5417 a3ec19ca. (https://medium.com/husarion-blog/batteries-choose-the-right-power-source-for-your-robot-5417a3ec19ca) [Accessed: 16-Jan-2019]

## Appendix A: Disposition Agreement

Auburn University’s IEEE SoutheastCon 2019 Hardware Competition Team is funded solely by donations generously given to the Student Projects and Research Committee and the Department of Electrical and Computer Engineering. Henceforth, all hardware is the property of the department and SPARC. At the conclusion of the projects, the hardware will be used for demonstrations or future SPARC projects.

Signature: | Date: 1/22/2019
Signature: | Date: 1/22/2019
Signature: | Date: 1/22/2019
Signature: | Date: 1/22/2019

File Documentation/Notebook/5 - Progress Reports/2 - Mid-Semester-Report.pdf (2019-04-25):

# Senior Design Mid-Semester Report

# IEEE SoutheastCon Hardware Competition

# Auburn University

# March 20, 2019

Matthew Castleberry, Joe Hinely, Josh Jabłonowski, Nia Perkins

## Project Overview

The purpose of this project is to create a robot to compete in the 2019 IEEE
SoutheastCon held in Huntsville, AL. The purpose of the conference is to share and demonstrate technical advancements in engineering. We will be competing in the hardware competition against other universities from across the southeastern US.
The purpose of the robot is to move around a square carpeted area with a side length of 244 centimeters, and pick up small objects on the field and place them into one of four colored home bases based on the color of the object. The arena will be split into two zones. Zone one features four home bases corresponding to four different colors. The robot will start in one of the four home bases. Zone two is separated by a one-inch thick white line. Zone two is where twelve objects will be placed for the robot to pick up: eight two inch wooden cubes, and four 2.5 inch diameter pit balls. The arena will feature a wooden box in the middle that will serve as an obstacle as well as four LED lights situated at the edge of zone two on the one-inch line. The four home bases will be placed at the four corners of the arena in zone one. An arena was built in order to test the robot as shown in Figure 1. This allows testing of the robot in a controlled area leading up to the competition.
The robot has several constraints that limit the size of the robot, materials used in the construction that assure the safety of participants and other robots [1]. The robot’s width and length must be within a nine by nine-inch area and a max height of eleven inches. The nine by nine area must include a bumper covering eighty percent of the perimeter. The bumper must be 1.5 inches from the ground and have a minimum vertical cover of one inch, and must not have a radius of curvature less than one centimeter. This is to prevent damage to the arena and other robots in the event of a collision. The robot can also raise a mechanical arm, with a max length of three inches, with a flag presenting the competing school’s name.
The robot utilizes a Raspberry Pi chip to control the motors while using an attached camera to identify the color and shape of the objects on the field. A LIDAR is used to localize the robot on the arena to help avoid the four lights and the wooden box in the middle of the arena. The robot will move the objects to the appropriate home base by running over the objects, closing a small door on the front of the robot so the robot can go back without losing any objects, hold them under the robot and move towards the appropriate home base of the object.


Figure 1: Field Constructed in Broun Hall room 368

## Technical Progress

### Mechanical Updates

Figure 2: Initial Design Robot

During the testing of the robot, the stepper motors for the front gate were run using a basic program to make them turn. During this test it was discovered that the rubber tubing connecting the stepper motors to the threaded poles was not tight enough, allowing the motors to slip through the tubing. This, alongside the front gate making the robot front heavy lead to the decision to remove the stepper motors and front gate completely. The front gate can be seen in Figure 2 with the pink 3D printed material and the two servo motors on top. In its place, a servo motor will be mounted onto the side of the robot and attached to a paddle that will lift up to allow objects underneath the robot as shown in Figure 3.
The servo motor not only solves the connection problem of the stepper motors but is considerably easier to program. Removing the added weight from the stepper motors at the top of the gate also lowered the center of gravity. This allows the robot to make more sudden stops and maneuver easier around the obstacles on the field.


Figure 3: Final Robot Design with servo

### Electrical Hardware Updates


Figure 4: Electrical Block Diagram

Since the start of our robot build, the electrical hardware design has made significant changes. In Figure 4 above, an obvious change from our previous designs is the placement of our components and addition to a control panel for adjusting settings and controlling the robot without direct access to the Raspberry Pi UI.
We’ve added switches for both batteries so that they can be switched on individually and electrically separate the 12V and 5V rails. An LCD screen will be used for output, programmable via a DIP switch package immediately next to it. LED lights were initially considered, but it was decided that they would take up too much GPIO on the Pi vs. a serial connection with an LCD screen.
Some mechanical changes were also made to our design, requiring some of the electrical hardware to change. Specifically, the three stepper motor controllers to control the gate have been replaced with servos, so no motor controllers are necessary- and will reduce the size of our protoboard/PCB.
A PCB design was started to sit on top of the Raspberry Pi to help integrate all of our components onto one board, shown in Figure 5 However, during the design phase it was decided that changes may need to be made closer to the competition that would exceed the time required for lead time to acquire and design a new PCB. Thus, a custom protoboard will be constructed instead that will still sit on top of the Pi- shown in Figure 6.


Figure 5: Pi HAT PCB Design (Unfinished)

Figure 6: Pi HAT Current Protoboard

Extra sensors have also been added to our electrical design to account for ROS requiring more input for accurate navigation. The IMU function is described below in the next section, but it will be integrated on the protoboard with a serial connection to the Raspberry Pi. Encoders are also being added to the motors, but they will not fit on our current prototype and will need to be integrated to the second robot.

## Software

### Robot Operating System (ROS)

The need for a simplified approach for localization sparked the switch to use the Robot Operating System (ROS.) ROS greatly simplifies complex localization, mapping, and pathfinding algorithms; all of which are incredibly essential to this competition, although, heed was taken at first because of the vast learning curve coupled with ROS. A very layman's explanation of ROS is that sensor data is input nodes, which house all the vital information for the sensors such as programs, readme files, or launch files. Nodes can talk to each other and request information, process the information, and send to another node. A graphical explanation of how our sensor nodes will communicate is shown in Figure 7 below. We have four sensors; LIDAR, Camera, IMU, and encoders that create four ROS nodes. The LIDAR, IMU, and Encoder nodes all input into the localization node, this node coupled with the camera node create what we call the decision maker or essentially a path planner. The decision maker then outputs motor control commands to move the robot.


Figure 7: ROS Node Diagram

### LIDAR and Localization

The LIDAR sensor is one of the main components of localization; this sensor acts sort of like a GPS for the robot. The YDLIDAR has a 360-degree scanning range with a 10-meter range. As stated previously and shown in Figure 7 the LIDAR will be a node, and this will be one of three inputs into the localization node. ROS greatly simplifies the localization process as it already has the algorithms needed, one being AMCL. Adaptive Monte Carlo localization is the process of tracking the pose of a robot against a known map, which is our case. AMCL takes in a map, LIDAR scan, and transform messages, and outputs pose estimates. As stated one of the first things we need to implement the AMCL algorithm is a known map, which is the competition field. We created a jpeg image which was feed thru a python program that was launched within ROS, and this gave us our map. However errors are being given when adding the LIDAR scan data to the map, we are currently debugging this error the next step will be to apply algorithms.

### Inertial Measurement Unit (IMU)

An inertial measurement unit (IMU) is a sensor that can measure nine degrees of freedom (9DOF). It has a combination of three three-axis sensors: gyroscope, accelerometer, and magnetometer. These sensors measure gravitational tilt, translational acceleration, and magnetic fields respectively. The IMU we have chosen has a well supported ROS library. It will be used as an input for the localization node. We originally did not recognize it as a required sensor but after further researching ROS, we are now implementing it. The demo program provided online is able to display the sensor orientation on a display. We verified this program worked with our hardware. We also verified that we can receive the raw sensor messages where needed in ROS.

### Rotary Encoder

In order to have more precise measurements in movement, we will use two capacitive encoders attached to the motors. The encoders will measure and count the turns of the motors, allowing us to know how far the robot will travel with one motor turn. Using this alongside the localization and object detection, we will be able to move the robot the exact distance towards any detected object to ensure the robot picks up the object. This will also prevent the robot from pushing any object into a position that would make it difficult to pick up.

### Visual Detection

We are using the Raspberry Pi Camera to detect the debris objects. By using the open-source computer vision library, the Pi can extrapolate the debris’s pixel location, pixel size, the angle from center, color, type, and approximate distance from the robot. It uses this data to make decisions on where the robot should go. For E-Day, we demonstrated that the robot can turn towards an object, drive until the object is right in front of it and then turn and find a different object. The program worked really well. The biggest issue is that the camera was pointed too far up and needed to be mounted at a lower angle. The only other issue was that it had some minor false detections but those should easily be easy to eliminate with more accurate tuning.

The next step is integrating visual detection with ROS. A custom message group has been created to pass the object information to the main group but needs to be tested. Once this is completed, it can be integrated with the localization in order to construct the competition algorithms.

## Budget

The budget for this project has remained the same- however the first report did not include parts that were needed for the second phase of the project and the second robot. The items bought for that are in the Table 1.

Description | Cost | Quantity | Line Price
2020 tubing 20mmX20mm | $0.16 | 96 | $15.36
100x Frame screws | $9.90 | 1 | $9.90
flanged bearings for axles | $3.97 | 8 | $31.76
Shaft collars for axles | $3.89 | 8 | $31.12
Axle | $7.72 | 1 | $7.72
Sprocket | $13.85 | 2 | $27.70
Motor | $7.25 | 2 | $14.50
Gearbox for motors | $45.90 | 2 | $91.80
Motor mounts | $6.50 | 2 | $13.00
Dual DC Motor Controller 5-36V | $63.39 | 1 | $63.39
LIDAR | $99.00 | 1 | $99.00
Capacitive Encoder | $21.86 | 2 | $43.72
Servo | $17.89 | 2 | $35.78
Pi Cam Cable | $5.43 | 1 | $5.43
LCD | $9.79 | 2 | $19.58
PLA pro orange | $22.99 | 1 | $22.99
PLA pro blue | $21.99 | 1 | $21.99
| | | $554.74
Table 1: Second Robot Costs

As to be expected with a project that is subject to change as better parts and ideas become available, the actual cost of development is different from that of the estimated budget for the original parts. The current actual cost of parts ordered to date is lined out below in Table 2.

Part | Quantity | Price/per | Total
2020 Extrusion | 196 | $0.21 | $41.16
Stepper Motor Controllers | 5 | $8.99 | $44.95
Raspberry Pi 3 | 2 | $48.99 | $97.98
Lithium Motor Grease | 1 | $8.76 | $8.76
Rubber Bands | 1 | $5.49 | $5.49
DC Motor Controller | 2 | $63.39 | $126.78
OpenMV Cam | 1 | $65.00 | $65.00
32GB microSD | 2 | $8.15 | $16.30
Triple Axis Gyro | 1 | $14.95 | $14.95
Pi Cam Cable | 2 | $5.43 | $10.86
Encoders | 4 | $21.86 | $87.44
Neoprene Rubber Strip | 1 | $0.96 | $0.96
Lipo 11.1V 5000mAH | 1 | $39.99 | $39.99
Lipo 7.4V 2200mAH | 1 | $18.99 | $18.99
Stepper Motors | 3 | $12.99 | $38.97
USB Cables | 1 | $6.99 | $6.99
Epoxy Paste | 1 | $8.79 | $8.79
2020 Frame Screws | 2 | $9.90 | $19.80
Flanged bearings for axles | 16 | $3.97 | $63.52
Shaft collars for axles | 16 | $3.89 | $62.24
Axle | 2 | $7.72 | $15.44
Sprocket | 4 | $13.85 | $55.40
Motor | 4 | $7.25 | $29.00
Gearbox | 4 | $45.90 | $183.60
Motor Mounts | 6.5 | $4.00 | $26.00
LIDAR | 2 | $99.00 | $198.00
Servos | 2 | $17.89 | $35.78
LCD | 1 | $9.79 | $9.79
PLA Orange | 1 | $22.99 | $22.99
PLA Blue | 1 | $21.99 | $21.99

2020 Nuts | 50 | $0.21 | $10.50
Various Screws | 1 | $17.92 | $17.92
Nema Screws | 1 | $4.18 | $4.18
Hex Nuts | 2 | $2.14 | $4.28
Lead Screws | 1 | $5.14 | $5.14
Lead Screw Tubing | 1 | $7.00 | $7.00
Gearbox mount accessories | 2 | $4.50 | $9.00
Chain | 1 | $16.88 | $16.88
Smaller Stepper Motors | 2 | $10.98 | $21.96
Chain tools | 1 | $21.80 | $21.80
| | ACTUAL COST | $1,496.57
Table 2: Total Robot Costs to Date

This is technically $300 over budget for just the parts we initially expected to buy, but we anticipated spending a bit more during development until we determined the parts we wanted to use as we experimented. We found this amount reasonable considering the progress we have made.

## Distribution of Tasks

The work done during the Spring 2019 semester can be split into four different task groups. Since there are seven total members between senior design and SPARC, it works well to have two members devoted to each task group. Matthew and William are focused on OpenCV and visual processing. Nia and Noah are focused on ROS and localization. Josh and Joe are focused on electrical hardware. Alex and Josh are focused on mechanical hardware.

## Timeline

Table 3 lists the tasks to be completed before the competition. Figure 8 summarizes the table in the form of a Gantt chart. Referencing the Gantt chart we are in cycle 2 of 3 and about a week behind the projected schedule. We plan to have the individual tasks complete by Wednesday, March 27th. The remaining week and a half before the competition will be used for integration and testing. The third phase will take place after the competition and will be focused on preparing for the final presentation.


Figure 8: Gantt Chart of Cycles 2 and 3

Task Name | Version* | Category | Deadline | Assignee
Construct 9”x9”x11” interior sizing box | 2 | Mechanical | April 1st | Alex
Mounting hole improvements on Electronics plate | 2 | Mechanical | March 22nd | Josh
Fabricate, 3D Print, Assemble, and Wire New Robot | 2 | Mechanical/El ectrical | March 27th | Full Team
Main and Auxilary Battery Voltage Detection | 2 | Electrical/ Software | April 1st | Joe
Wire Encoders | 2 | Electrical | March 27th | Joe
Design and Build Control Panel | 1 and 2 | Electrical | March 27th | Josh
Integrate Serial Control in ROS | 1 | Software | March 27th | William
ROS Localization | 1 | Software | March 27th | Nia/Noah
Capture ROS bag | 1 | Software | March 27th | Nia/Noah
Integrate Visual Detection in ROS | 1 | Software | March 25th | Matthew
Integrate Encoders in ROS | 1 | Software | April 1st | Nia/Noah
Test and Tune Full Competiton Algorithm (With 1 robot) | 1 | Software | April 5th | Full Team
Test and Tune Full Competiton Algorithm (With 2 robots on the field) | 1 and 2 | Software | April 12th | Full Team

Table 3: List of Tasks to be Completed

## Conclusion

Overall, we are constructing a robot to autonomously move small blocks and balls into coordinated colored corners. The technical deadline for this project is April 12th. The operating technical budget is $715 for version 1 of the robot and $555 for the remaining parts for the second version.

## References

[1] “2019 SoutheastCon Hardware Rules v1.3.” IEEE, Huntsville, 18-Aug-2018. “http://sites.ieee.org/southeastcon2019/files/2019/02/2019-SoutheastCon-HW-Rules_v1_3-1.pdf ”

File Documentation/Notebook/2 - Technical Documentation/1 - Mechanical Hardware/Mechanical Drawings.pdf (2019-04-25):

## Mechanical Drawings

*All drawings were composed using the student version of SolidWorks 2018-2019


Figure 1: Isometric View


Figure 2: Top View

Figure 3: Bottom View


Figure 4: Right View

Figure 5: Left View


Figure 6: Back View

Figure 7: Front View


Figure 8: 8020 Frame

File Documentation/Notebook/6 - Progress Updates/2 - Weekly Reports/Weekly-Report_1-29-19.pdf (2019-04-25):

# Weekly Report - Tuesday, January 29, 2019

Auburn University IEEE SoutheastCon 2019 Hardware Competition Team

## Current Development Tasks

Task Name | Category | % Compl. | Progress Updates
LIDAR Localization Algorithm Development | Software | 5% | Researching & brainstorming begun.
Electrical Hardware Selection | Electrical | 80% | New camera, motor controllers, and batteries have been ordered- expected arrival this week. Encoders for motors are still being considered.
Electrical Hardware Placement | Electrical-Mechanical Integration | 5% | First robot will be able to be mostly assembled by the end of the week for testing-barring timely arrival of parts. Will compile wiring diagram this week with specific parts
Visual Processing Real-Time Analysis | Software | 70% | The original program developed has a latency of ~1.8s. After some improvements, the latency was reduced to ~0.3s. Further testing is needed to determine if this is enough of an improvement.
Visual Processing Alternatives Analysis | Electrical/ Software | 50% | Some alternatives are being considered to using the OpenCV+PiCam. We purchased the OpenMV camera and will directly compare its performance to the current method.

## Senior Design Team Members Time Management

Member Name | Task Name | ~ Hours Spent
All Members | Team Meetings | 2.5
Matthew Castleberry | Visual Processing Real-Time Analysis | 7

Matthew Castleberry | Visual Processing Alternatives Analysis | 3
Nia Perkins | LIDAR Localization Algorithm Development | 2
Joe Hinely | Electrical Hardware Selection | 1.5
Josh Jablonowski | Electrical Hardware Selection | 2

## Achievements, Obstacles, and Risks

The major obstacles to the vision detection aspect to the software is the latency. The higher the latency, the slower the robot can understand its surroundings. In order to ensure a high success in the competition, we must maximize the speed at which it can accurately short the debris. There are currently three solutions to solving the low latency issue: improve the original algorithm with the Raspberry Pi and Pi Cam, use a programmable camera module like the OpenMV or Pixy 2 Cam, or replace the Raspberry Pi with a faster single board computer like the LattePanda. We achieved a significant improvement with the optimized algorithm but it may not be better than the capability of the OpenMV camera. A new single board computer with a significant improvement from the Pi costs $150 to $350 whereas the OpenMV camera costs approximately $60. We purchased the OpenMV camera. Hopefully, it will come in during the next week or two.
The LIDAR is used for robot localization. This is done by the LIDAR outputting numerous points that need to be interpreted into a static graph. This is causing a bit of an issue because the LIDAR’s center point moves with the robot. We found an article where a group of students used a LIDAR sensor to plan a path with an indoor ATV, on a set grid. We will use this article as much as we can, however, in the article, they had one set start and end location where ours can change. We are still seeking outside help.
Electrical hardware has been chosen and purchased for the first prototype robot. We’re confident in the parts that we have ordered, but it is possible we may run into issues. Consideration is being taken into account over buying motor encoders to provide data on actual motor speeds. We intend to have the robot wired to working condition by the end of the week given the parts arrive before Friday. We started brainstorming ideas to integrate the electrical parts with proper mounts on the mechanical frame.

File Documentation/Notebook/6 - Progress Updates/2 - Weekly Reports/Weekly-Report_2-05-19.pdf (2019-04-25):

# Weekly Report - Tuesday, February 05, 2019

Auburn University IEEE SoutheastCon 2019 Hardware Competition Team

## Current Development Tasks

Task Name | Category | % Compl. | Progress Updates
LIDAR Localization Algorithm Development | Software | 10% | Pseudocode has begun for the LIDAR algorithm. Will start looking into ROS prebuilt algorithms.
Electrical Hardware Selection | Electrical | 95% | Parts ordered last week arrived. Encoders for motors are still being considered.
Electrical Hardware Placement | Electrical-Mechanical Integration | 15% | Creating temporary wiring on breadboard to get the prototype running. Component placement CAD is being worked on, while placing actual components in parallel
Motor Controller Integration | Electrical-Software Integration | 50% | Stepper motors and DC motor controller have been connected to an Arduino and tested. The next step is being able to control them from a Raspberry Pi through the Arduino.
Raspberry Pi Cam Visual Processing Real-Time Analysis | Software | 100% | Algorithm improvements and reducing resolution to 640x480 increased 0.5 FPS to 3.5 FPS. Reducing resolution to 320x240 increases it to 20 FPS but accuracy is reduced.
Open MV Cam Visual Processing Real-Time Analysis | Electrical/ Software | 70% | Received camera last week. Example program has functionality very similar to the existing algorithm. Needs tuning and integration with Pi to compare performance.
Follow Debris Algorithm | Software | 40% | Test platform can rotate towards largest debris. Needs to be converted to proportional control. We need a way to

check distance to object.

## Senior Design Team Members Time Management

Member Name | Task Name | ~ Hours Spent
All Members | Team Meetings | 1.5
Matthew Castleberry | Raspberry Pi Cam Visual Processing Real-Time Analysis | 2
Matthew Castleberry | Open MV Cam Visual Processing Real-Time Analysis | 1
Matthew Castleberry | Follow Debris Algorithm | 3
Matthew Castleberry | Motor Controller Integration | 1
Nia Perkins | LIDAR Localization Algorithm Development | 2
Joe Hinely | Electrical Hardware Selection | 2
Joe Hinely | Electrical Hardware Placement | 0.5
Josh Jablonowski | Electrical Hardware Selection | 1
Josh Jablonowski | Electrical Hardware Placement | 3
Josh Jablonowski | Motor Controller Integration | 1

## Achievements, Obstacles, and Risks

All electrical parts that were initially anticipated have been ordered- current efforts are being put into getting the physical prototype running while developing CAD design for the 3D printed parts to properly mount all components. Potential obstacles to completing the first prototype this by the end of next week include 3D printer failure, component failure, and wiring difficulties.
The visual processing algorithm is working much faster than it had in the past making it a viable option. We are still considering the OpenMV camera and will be doing development in parallel with both cameras so that their performance can be compared. We tested the program to point the test platform toward a cube and it worked but it needs some improvement and tuning. At this point, we are ready to test the algorithm on the main bot once the electrical hardware is completed. Another aspect that will be in development this week is to be able to determine the approximate distance from the camera to an object based on the known dimensions.
Last week’s brainstorming has placed us at our current step which is planning out our pseudocode for determining how the robot will self locate. We also determined that we need a short script file that will put the date the LIDAR outputs into two separate arrays one for distance and the other angles. That script file & the pseudocode will be written in the upcoming week. We are thinking about using Robot Operating System (ROS) to help with localization. We will attempt to test the ROS library provided by the LIDAR manufacturer to see if this is the route we should take. We also have found many similar projects online that use a 3-axis magnometer, accelerometer, and gyroscope in a 9 degree of freedom (DoF), inertial measurement unit (IMU) sensor. We have scheduled a visit with one of Dr. Roppel’s grad students in the RFID Lab on Wednesday at 3 PM. They have a robot running ROS on a Pi with a 9DoF IMU and LIDAR.

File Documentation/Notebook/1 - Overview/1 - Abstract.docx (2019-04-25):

Abstract

Professors: Dr. Dean, Dr. Roppel

Team Members: Matthew Castleberry, Josh Jablonowski, Joe Hinely, Nia Perkins

Description: A joint project with the Student Projects and Research Committee (SPARC) to design, build, and compete an autonomous robot to collect and sort colored cubes and balls into corresponding colored corners of a small square shaped arena.


(Full Competition Team) Left to Right: Matthew Castleberry, Nia Perkins, Alex Jones, Noah Niedzwiecki, Rebecca Thomas, Joe Hinely, William Yates, Josh Jablonowski


Output of image processing algorithms determining positions of objects on field with respect to robot.

Localization map indicating position and orientation of robot within arena


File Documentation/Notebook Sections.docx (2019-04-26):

Image result for student projects and research committee

IEEE Southeastcon hardware competition

## Spring 2019 Senior Design

Senior Design Project Notebook

### Matthew Castleberry, Josh JABLONOWSKI, JOE hinley, nia perkins

##### [Click here to enter a date]

| IEEE SOUTHEASTCON Senior Design Notebook

| IEEE SOUTHEASTCON Senior Design Notebook

| IEEE SOUTHEASTCON 2019 Senior Design Notebook

| IEEE SOUTHEASTCON Senior Design Notebook

IN THIS SECTION:

- Abstract
- Project overview

## Overview


1

Senior Design Project Notebook


IN THIS SECTION:

- Mechanical Hardware
- Electrical Hardware
- Software

## Technical Documentation

2

Senior Design Project Notebook

IN THIS SECTION:

- Post Competition Project Review
- Future Work

## Competition Details


Senior Design Project Notebook

3

IN THIS SECTION:

- Budget
- Bill of Materials
- Purchase Orders
- Relationship Between SPARC and Senior Design

## Administrative Documentation


4

Senior Design Project Notebook

IN THIS SECTION:

- Project Proposal
- Mid-Semester Report
- Final Report

## Progress Reports

Senior Design Project Notebook

5


IN THIS SECTION:

- Fall Meeting Notes
- Spring Weekly Reports

## Progress Updates

Senior Design Project Notebook


6


Senior Design Project Notebook

7

IN THIS SECTION:

- A: Datasheets
- B: Source Code

## Appendices

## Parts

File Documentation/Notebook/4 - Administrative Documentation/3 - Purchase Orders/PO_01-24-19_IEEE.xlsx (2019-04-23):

Purchase Order Form
Student Projects and Research Committee
 | Category/Project: | IEEE SouthEastCon 2019 |  | Request Date: | 01/24/Y19
 | Requester: | Joshua Jablonowski |  | Estimated Total Cost: | $256.91
 | Vice President: | Matthew Castleberry
 | Faculty Advisor: | Dr. Thaddeus Roppel
Item # | Vendor | Description | Measurement/Spec. | Cost | Quantity | Line Price | URL
1 | Amazon | BIQU Stepper Motor Controller | 5 | $8.99 | 1 | $8.99 | https://www.amazon.com/BIQU-Compatible-Stepper-StepStick-Controller/dp/B01FFGAKK8
2 | Amazon | LiPo Battery 11.1V 5000mAH 50C |  | $39.99 | 1 | $39.99 | https://www.amazon.com/HRB-50C-100C-Quadcopter-Airplane-Helicopter/dp/B06XNQGZY6
3 | Amazon | Raspberry Pi3+Power Supply+Heatsink |  | $48.99 | 1 | $48.99 | https://www.amazon.com/CanaKit-Raspberry-Power-Supply-Listed/dp/B07BC6WH7V?s=pc
4 | Amazon | Lithium Motor Grease | 1lb | $8.76 | 1 | $8.76 | https://www.amazon.com/Mag-134-Multi-Purpose-Lithium-Grease/dp/B000HMOXD6?s=automotive
5 | Amazon | Rubber Bands | Assorted Size | $5.49 | 1 | $5.49 | https://www.amazon.com/AmazonBasics-Assorted-Color-Rubber-Bands/dp/B074B1KCXD?s=office-products
6 | RobotShop | Dual DC Motor Controller 5-36V |  | $63.39 | 1 | $63.39 | https://www.robotshop.com/en/smartdriveduo-smart-dual-channel-30a-motor-driver.html
7 | SEEED Studio | OpenMV Cam M7 |  | $65.00 | 1 | $65.00 | https://www.seeedstudio.com/OpenMV-Cam-M7-p-2855.html
8 | Amazon | 32GB microSD HC | 2 | $16.30 | 1 | $16.30 | https://www.amazon.com/SanDisk-MicroSD-Ultra-UHS-1-Memory/dp/B00CNYV942
 |  |  |  | $0.00 |  | $0.00
 |  |  |  | $0.00 |  | $0.00
 |  |  |  | $0.00 |  | $0.00
 |  |  |  | $0.00 |  | $0.00
 |  |  |  | $0.00 |  | $0.00
 |  |  |  | $0.00 |  | $0.00
 |  |  |  | $0.00 |  | $0.00
 |  |  |  | $0.00 |  | $0.00
 |  |  |  | $0.00 |  | $0.00
 |  |  |  | $0.00 |  | $0.00
 |  |  |  | $0.00 |  | $0.00
 |  |  |  | $0.00 |  | $0.00
 |  |  |  | $0.00 |  | $0.00
 |  |  |  | $0.00 |  | $0.00
 |  |  |  | $0.00 |  | $0.00
 |  |  |  | $0.00 |  | $0.00
 |  |  |  | $0.00 |  | $0.00
 |  |  |  | $0.00 |  | $0.00
 |  |  |  | $0.00 |  | $0.00
 |  |  |  | $0.00 |  | $0.00
 |  |  |  | $0.00 |  | $0.00
 |  |  |  | $0.00 |  | $0.00
 |  |  |  | $0.00 |  | $0.00
 |  |  |  | $0.00 |  | $0.00
 |  |  |  | $0.00 |  | $0.00
 |  |  |  | $0.00 |  | $0.00
 |  |  |  | $0.00 |  | $0.00
 |  |  |  | $0.00 |  | $0.00
 |  |  |  | $0.00 |  | $0.00
 |  |  |  | $0.00 |  | $0.00

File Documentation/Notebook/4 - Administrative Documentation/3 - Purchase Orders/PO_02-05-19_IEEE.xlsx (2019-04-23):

Purchase Order Form
Student Projects and Research Committee
 | Category/Project: | IEEE Southeastcon |  | Request Date: | 2019-02-05
 | Requester: | Matthew Castleberry |  | Estimated Total Cost: | $65.06
 | Vice President: | Matthew Castleberry
 | Faculty Advisor: | Dr. Thaddeus Roppel
Item # | Vendor | Description | Measurement/Spec. | Cost | Quantity | Line Price | URL
B01HNA1A6M | Amazon | L3GD20H Triple-Axis Gyro Breakout Board |  | $14.95 | 1 | $14.95 | https://www.amazon.com/dp/B01HNA1A6M
B00I6LJ19G | Amazon | Pi Cam Cable | 12" | $5.43 | 1 | $5.43 | https://www.amazon.com/dp/B00I6LJ19G/
AMT103-V | Arrow | Capacitive Encoder |  | $21.86 | 2 | $43.72 | https://www.arrow.com/en/products/amt103-v/cui-inc
90125K56 | McMasterCarr | Multipurpose Neoprene Rubber Strip | 1/2" Wide, 1/8" Thick 10ft long | $0.96 | 1 | $0.96 | https://www.mcmaster.com/90125k56
 |  |  |  | $0.00 |  | $0.00
 |  |  |  | $0.00 |  | $0.00
 |  |  |  | $0.00 |  | $0.00
 |  |  |  | $0.00 |  | $0.00
 |  |  |  | $0.00 |  | $0.00
 |  |  |  | $0.00 |  | $0.00
 |  |  |  | $0.00 |  | $0.00
 |  |  |  | $0.00 |  | $0.00
 |  |  |  | $0.00 |  | $0.00
 |  |  |  | $0.00 |  | $0.00
 |  |  |  | $0.00 |  | $0.00
 |  |  |  | $0.00 |  | $0.00
 |  |  |  | $0.00 |  | $0.00
 |  |  |  | $0.00 |  | $0.00
 |  |  |  | $0.00 |  | $0.00
 |  |  |  | $0.00 |  | $0.00
 |  |  |  | $0.00 |  | $0.00
 |  |  |  | $0.00 |  | $0.00
 |  |  |  | $0.00 |  | $0.00
 |  |  |  | $0.00 |  | $0.00
 |  |  |  | $0.00 |  | $0.00
 |  |  |  | $0.00 |  | $0.00
 |  |  |  | $0.00 |  | $0.00
 |  |  |  | $0.00 |  | $0.00
 |  |  |  | $0.00 |  | $0.00
 |  |  |  | $0.00 |  | $0.00
 |  |  |  | $0.00 |  | $0.00
 |  |  |  | $0.00 |  | $0.00
 |  |  |  | $0.00 |  | $0.00
 |  |  |  | $0.00 |  | $0.00
 |  |  |  | $0.00 |  | $0.00
 |  |  |  | $0.00 |  | $0.00
 |  |  |  | $0.00 |  | $0.00
 |  |  |  | $0.00 |  | $0.00

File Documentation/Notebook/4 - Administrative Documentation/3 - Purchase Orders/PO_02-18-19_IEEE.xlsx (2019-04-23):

Purchase Order Form
Student Projects and Research Committee
 | Category/Project: | IEEE Southeastcon |  | Request Date: | 2019-02-18
 | Requester: | Matthew Castleberry |  | Estimated Total Cost: | $87.93
 | Vice President: | Matthew Castleberry
 | Faculty Advisor: | Dr. Thaddeus Roppel
Item # | Vendor | Description | Measurement/Spec. | Cost | Quantity | Line Price | URL
B06XNQGZY6 | Amazon | LiPo Battery 11.1V 5000mAH 50C |  | $39.99 | 1 | $39.99 | https://www.amazon.com/dp/B06XNQGZY6/
B0072AEWTG | Amazon | LiPo Battery 2S 2200mAh 25C |  | $18.99 | 1 | $18.99 | https://www.amazon.com/dp/B0072AEWTG
B075J8CP7Y | Amazon | Short Body Nema 17 Stepper Motor |  | $10.98 | 2 | $21.96 | https://www.amazon.com/dp/B075J8CP7Y/
B01NAT82AC | Amazon | 9" Mini USB Cable Mini USB Right Angle |  | $6.99 | 1 | $6.99 | https://www.amazon.com/dp/B01NAT82AC/
 |  |  |  | $0.00 |  | $0.00
 |  |  |  | $0.00 |  | $0.00
 |  |  |  | $0.00 |  | $0.00
 |  |  |  | $0.00 |  | $0.00
 |  |  |  | $0.00 |  | $0.00
 |  |  |  | $0.00 |  | $0.00
 |  |  |  | $0.00 |  | $0.00
 |  |  |  | $0.00 |  | $0.00
 |  |  |  | $0.00 |  | $0.00
 |  |  |  | $0.00 |  | $0.00
 |  |  |  | $0.00 |  | $0.00
 |  |  |  | $0.00 |  | $0.00
 |  |  |  | $0.00 |  | $0.00
 |  |  |  | $0.00 |  | $0.00
 |  |  |  | $0.00 |  | $0.00
 |  |  |  | $0.00 |  | $0.00
 |  |  |  | $0.00 |  | $0.00
 |  |  |  | $0.00 |  | $0.00
 |  |  |  | $0.00 |  | $0.00
 |  |  |  | $0.00 |  | $0.00
 |  |  |  | $0.00 |  | $0.00
 |  |  |  | $0.00 |  | $0.00
 |  |  |  | $0.00 |  | $0.00
 |  |  |  | $0.00 |  | $0.00
 |  |  |  | $0.00 |  | $0.00
 |  |  |  | $0.00 |  | $0.00
 |  |  |  | $0.00 |  | $0.00
 |  |  |  | $0.00 |  | $0.00
 |  |  |  | $0.00 |  | $0.00
 |  |  |  | $0.00 |  | $0.00
 |  |  |  | $0.00 |  | $0.00
 |  |  |  | $0.00 |  | $0.00
 |  |  |  | $0.00 |  | $0.00
 |  |  |  | $0.00 |  | $0.00

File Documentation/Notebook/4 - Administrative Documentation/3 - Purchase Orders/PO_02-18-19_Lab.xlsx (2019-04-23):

Purchase Order Form
Student Projects and Research Committee
 | Category/Project: | Lab Supplies |  | Request Date: | 2019-02-18
 | Requester: | Matthew Castleberry |  | Estimated Total Cost: | $55.28
 | Vice President: | Matthew Castleberry
 | Faculty Advisor: | Dr. Thaddeus Roppel
Item # | Vendor | Description | Measurement/Spec. | Cost | Quantity | Line Price | URL
B075WR9FVL | Amazon | 532pcs Heat Shrink Tubing Black |  | $8.37 | 1 | $8.37 | https://www.amazon.com/dp/B075WR9FVL/
B07B54QVZG | Amazon | Liquid Flux Water-Washable in 10ml Pen |  | $7.95 | 1 | $7.95 | https://www.amazon.com/dp/B07B54QVZG/
B00SW9JI9A | Amazon | HDMI to VGA Adapter |  | $7.99 | 1 | $7.99 | https://www.amazon.com/dp/B00SW9JI9A
B074X2GDH2 | Amazon | AUSTOR 36 Pieces Double Sided PCB |  | $11.99 | 1 | $11.99 | https://www.amazon.com/dp/B074X2GDH2/
B013ZWM1F6 | Amazon | Hilitchi 360pcs Brass Standoff Kit | M2 M3 M4 | $18.98 | 1 | $18.98 | https://www.amazon.com/dp/B013ZWM1F6/
 |  |  |  | $0.00 |  | $0.00
 |  |  |  | $0.00 |  | $0.00
 |  |  |  | $0.00 |  | $0.00
 |  |  |  | $0.00 |  | $0.00
 |  |  |  | $0.00 |  | $0.00
 |  |  |  | $0.00 |  | $0.00
 |  |  |  | $0.00 |  | $0.00
 |  |  |  | $0.00 |  | $0.00
 |  |  |  | $0.00 |  | $0.00
 |  |  |  | $0.00 |  | $0.00
 |  |  |  | $0.00 |  | $0.00
 |  |  |  | $0.00 |  | $0.00
 |  |  |  | $0.00 |  | $0.00
 |  |  |  | $0.00 |  | $0.00
 |  |  |  | $0.00 |  | $0.00
 |  |  |  | $0.00 |  | $0.00
 |  |  |  | $0.00 |  | $0.00
 |  |  |  | $0.00 |  | $0.00
 |  |  |  | $0.00 |  | $0.00
 |  |  |  | $0.00 |  | $0.00
 |  |  |  | $0.00 |  | $0.00
 |  |  |  | $0.00 |  | $0.00
 |  |  |  | $0.00 |  | $0.00
 |  |  |  | $0.00 |  | $0.00
 |  |  |  | $0.00 |  | $0.00
 |  |  |  | $0.00 |  | $0.00
 |  |  |  | $0.00 |  | $0.00
 |  |  |  | $0.00 |  | $0.00
 |  |  |  | $0.00 |  | $0.00
 |  |  |  | $0.00 |  | $0.00
 |  |  |  | $0.00 |  | $0.00
 |  |  |  | $0.00 |  | $0.00
 |  |  |  | $0.00 |  | $0.00

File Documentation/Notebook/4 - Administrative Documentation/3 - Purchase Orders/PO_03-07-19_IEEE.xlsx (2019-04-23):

Purchase Order Form
Student Projects and Research Committee
 | Category/Project: | IEEE Southeastcon |  | Request Date: | 2019-03-01
 | Requester: | Alex Jones |  | Estimated Total Cost: | $554.74
 | Vice President: | Matthew Castleberry
 | Faculty Advisor: | Dr. Thaddeus Roppel
Item # | Vendor | Description | Measurement/Spec. | Cost | Quantity | Line Price | URL
 | 80-20 | 2020 tubing 20mmX20mm | 96in | $0.16 | 96 | $15.36 | https://8020.net/20-2020.html
91239A148 | McMasterCarr | 100x Frame screws | m4 button head screw | $9.90 | 1 | $9.90 | https://www.mcmaster.com/91239a148
6383k213 | McMasterCarr | flanged bearings for axles | 6383k213 | $3.97 | 8 | $31.76 | https://www.mcmaster.com/6383k213
6436k131 | McMasterCarr | Shaft collars for axles | 6436k131 | $3.89 | 8 | $31.12 | https://www.mcmaster.com/6436k131
1327k66 | McMasterCarr | Axle | 0.25 dia x 12in long | $7.72 | 1 | $7.72 | https://www.mcmaster.com/1327k66
6280k351 | McMasterCarr | Sprocket | ANSI 35 Chain, 13 Teeth | $13.85 | 2 | $27.70 | https://www.mcmaster.com/6280k351
M5-RS550-12 | BaneBots | Motor | rs550 | $7.25 | 2 | $14.50 | http://www.banebots.com/product/M5-RS550-12.html
P61S-44 | BaneBots | Gearbox for motors | P61 Gearbox: Standard, 16:1 | $45.90 | 2 | $91.80 | http://www.banebots.com/product/P61S-44.html
P61B-H574 | BaneBots | Motor mounts | P61 Pinion and Motor Hardware Kit | $6.50 | 2 | $13.00 | http://www.banebots.com/product/P61B-H574.html
RB-Cyt-220 | RobotShop | Dual DC Motor Controller 5-36V |  | $63.39 | 1 | $63.39 | https://www.robotshop.com/en/smartdriveduo-smart-dual-channel-30a-motor-driver.html
RB-Ydl-01 | RobotShop | LIDAR | YDLIDAR X4 | $99.00 | 1 | $99.00 | https://www.robotshop.com/en/ydlidar-x4-360-laser-scanner.html
amt103- | Arrow | Capacitive Encoder |  | $21.86 | 2 | $43.72 | https://www.arrow.com/en/products/amt103-v/cui-inc
B076CNKQX4 | Amazon | Servo | DS3218MG | $17.89 | 2 | $35.78 | https://www.amazon.com/ANNIMOS-Digital-Waterproof-DS3218MG-Control/dp/B076CNKQX4
B00I6LJ19G | Amazon | Pi Cam Cable | 12" | $5.43 | 1 | $5.43 | https://www.amazon.com/dp/B00I6LJ19G/
B0711WLVP9 | Amazon | LCD | 16x2 | $9.79 | 2 | $19.58 | https://www.amazon.com/LGDehome-Interface-Adapter-Backlight-MEGA2560/dp/B0711WLVP9/
B01EKEMA2M | Amazon | PLA pro orange |  | $22.99 | 1 | $22.99 | https://www.amazon.com/eSUN-1-75mm-Orange-Printer-Filament/dp/B01EKEMA2M/
B01EKEMNRO | Amazon | PLA pro blue |  | $21.99 | 1 | $21.99 | https://www.amazon.com/eSUN-1-75mm-Printer-Filament-2-2lbs/dp/B01EKEMNRO/
 |  |  |  | $0.00 |  | $0.00
 |  |  |  | $0.00 |  | $0.00
 |  |  |  | $0.00 |  | $0.00
 |  |  |  | $0.00 |  | $0.00
 |  |  |  | $0.00 |  | $0.00
 |  |  |  | $0.00 |  | $0.00
 |  |  |  | $0.00 |  | $0.00
 |  |  |  | $0.00 |  | $0.00
 |  |  |  | $0.00 |  | $0.00
 |  |  |  | $0.00 |  | $0.00
 |  |  |  | $0.00 |  | $0.00
 |  |  |  | $0.00 |  | $0.00
 |  |  |  | $0.00 |  | $0.00
 |  |  |  | $0.00 |  | $0.00
 |  |  |  | $0.00 |  | $0.00
 |  |  |  | $0.00 |  | $0.00
 |  |  |  | $0.00 |  | $0.00
 |  |  |  | $0.00 |  | $0.00
 |  |  |  | $0.00 |  | $0.00
 |  |  |  | $0.00 |  | $0.00
 |  |  |  | $0.00 |  | $0.00

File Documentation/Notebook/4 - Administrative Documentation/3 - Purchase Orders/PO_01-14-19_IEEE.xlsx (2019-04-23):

Purchase Order Form
Student Projects and Research Committee
 | Category/Project: | IEEE 2019
 | Requester: | Alex Jones |  | Approved?
 | Vice President: | Matthew Castleberry
 | Faculty Advisor: | Dr. Thaddeus Roppel
 | Request Date: | 2019-01-14 | Vendor: | 8020
 | Estimated Total Cost: | $21.00
Item # | Description | Measurement/Spec. | Cost | Quantity | Line Price | URL
1 | M4 Slide-in Economy T-Nut Block | M4 | $0.21 | 100 | $21.00 | https://8020.net/14159.html
 |  |  | $0.00 |  | $0.00
 |  |  | $0.00 |  | $0.00
 |  |  | $0.00 |  | $0.00
 |  |  | $0.00 |  | $0.00
 |  |  | $0.00 |  | $0.00
 |  |  | $0.00 |  | $0.00
 |  |  | $0.00 |  | $0.00
 |  |  | $0.00 |  | $0.00
 |  |  | $0.00 |  | $0.00
 |  |  | $0.00 |  | $0.00
 |  |  | $0.00 |  | $0.00
 |  |  | $0.00 |  | $0.00
 |  |  | $0.00 |  | $0.00
 |  |  | $0.00 |  | $0.00
 |  |  | $0.00 |  | $0.00
 |  |  | $0.00 |  | $0.00
 |  |  | $0.00 |  | $0.00
 |  |  | $0.00 |  | $0.00
 |  |  | $0.00 |  | $0.00
 |  |  | $0.00 |  | $0.00
 |  |  | $0.00 |  | $0.00
 |  |  | $0.00 |  | $0.00
 |  |  | $0.00 |  | $0.00
 |  |  | $0.00 |  | $0.00
 |  |  | $0.00 |  | $0.00
 |  |  | $0.00 |  | $0.00
 |  |  | $0.00 |  | $0.00
 |  |  | $0.00 |  | $0.00
 |  |  | $0.00 |  | $0.00
 |  |  | $0.00 |  | $0.00
 |  |  | $0.00 |  | $0.00
 |  |  | $0.00 |  | $0.00
 |  |  | $0.00 |  | $0.00
 |  |  | $0.00 |  | $0.00
 |  |  | $0.00 |  | $0.00
 |  |  | $0.00 |  | $0.00
 |  |  | $0.00 |  | $0.00

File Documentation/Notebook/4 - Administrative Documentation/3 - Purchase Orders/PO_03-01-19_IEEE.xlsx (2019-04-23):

Purchase Order Form
Student Projects and Research Committee
 | Category/Project: | IEEE Southeastcon |  | Request Date: | 2019-03-01
 | Requester: | Matthew Castleberry |  | Estimated Total Cost: | $46.89
 | Vice President: | Matthew Castleberry
 | Faculty Advisor: | Dr. Thaddeus Roppel
Item # | Vendor | Description | Measurement/Spec. | Cost | Quantity | Line Price | URL
B07BDR5PDW | Amazon | Raspberry Pi 3 B+ |  | $38.10 | 1 | $38.10 | https://www.amazon.com/dp/B07BDR5PDW/
B000AB4A8M | Amazon | Two-Part Epoxy Adhesive Paste | 1/2 Pound | $8.79 | 1 | $8.79 | https://www.amazon.com/dp/B000AB4A8M/
 |  |  |  | $0.00 |  | $0.00
 |  |  |  | $0.00 |  | $0.00
 |  |  |  | $0.00 |  | $0.00
 |  |  |  | $0.00 |  | $0.00
 |  |  |  | $0.00 |  | $0.00
 |  |  |  | $0.00 |  | $0.00
 |  |  |  | $0.00 |  | $0.00
 |  |  |  | $0.00 |  | $0.00
 |  |  |  | $0.00 |  | $0.00
 |  |  |  | $0.00 |  | $0.00
 |  |  |  | $0.00 |  | $0.00
 |  |  |  | $0.00 |  | $0.00
 |  |  |  | $0.00 |  | $0.00
 |  |  |  | $0.00 |  | $0.00
 |  |  |  | $0.00 |  | $0.00
 |  |  |  | $0.00 |  | $0.00
 |  |  |  | $0.00 |  | $0.00
 |  |  |  | $0.00 |  | $0.00
 |  |  |  | $0.00 |  | $0.00
 |  |  |  | $0.00 |  | $0.00
 |  |  |  | $0.00 |  | $0.00
 |  |  |  | $0.00 |  | $0.00
 |  |  |  | $0.00 |  | $0.00
 |  |  |  | $0.00 |  | $0.00
 |  |  |  | $0.00 |  | $0.00
 |  |  |  | $0.00 |  | $0.00
 |  |  |  | $0.00 |  | $0.00
 |  |  |  | $0.00 |  | $0.00
 |  |  |  | $0.00 |  | $0.00
 |  |  |  | $0.00 |  | $0.00
 |  |  |  | $0.00 |  | $0.00
 |  |  |  | $0.00 |  | $0.00
 |  |  |  | $0.00 |  | $0.00
 |  |  |  | $0.00 |  | $0.00
 |  |  |  | $0.00 |  | $0.00
 |  |  |  | $0.00 |  | $0.00

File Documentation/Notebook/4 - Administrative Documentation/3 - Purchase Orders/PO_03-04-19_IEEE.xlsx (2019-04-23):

Purchase Order Form
Student Projects and Research Committee
 | Category/Project: | IEEE Southeastcon |  | Request Date: | 2019-03-01
 | Requester: | Matthew Castleberry |  | Estimated Total Cost: | $75.80
 | Vice President: | Matthew Castleberry
 | Faculty Advisor: | Dr. Thaddeus Roppel
Item # | Vendor | Description | Measurement/Spec. | Cost | Quantity | Line Price | URL
14001 | SparkFun | SparkFun 9DoF Razor IMU M0 |  | $35.95 | 2 | $71.90 | https://www.sparkfun.com/products/14001
14017 | SparkFun | Raspberry Pi GPIO Tall Header - 2x20 |  | $1.95 | 2 | $3.90 | https://www.sparkfun.com/products/14017
 |  |  |  | $0.00 |  | $0.00
 |  |  |  | $0.00 |  | $0.00
 |  |  |  | $0.00 |  | $0.00
 |  |  |  | $0.00 |  | $0.00
 |  |  |  | $0.00 |  | $0.00
 |  |  |  | $0.00 |  | $0.00
 |  |  |  | $0.00 |  | $0.00
 |  |  |  | $0.00 |  | $0.00
 |  |  |  | $0.00 |  | $0.00
 |  |  |  | $0.00 |  | $0.00
 |  |  |  | $0.00 |  | $0.00
 |  |  |  | $0.00 |  | $0.00
 |  |  |  | $0.00 |  | $0.00
 |  |  |  | $0.00 |  | $0.00
 |  |  |  | $0.00 |  | $0.00
 |  |  |  | $0.00 |  | $0.00
 |  |  |  | $0.00 |  | $0.00
 |  |  |  | $0.00 |  | $0.00
 |  |  |  | $0.00 |  | $0.00
 |  |  |  | $0.00 |  | $0.00
 |  |  |  | $0.00 |  | $0.00
 |  |  |  | $0.00 |  | $0.00
 |  |  |  | $0.00 |  | $0.00
 |  |  |  | $0.00 |  | $0.00
 |  |  |  | $0.00 |  | $0.00
 |  |  |  | $0.00 |  | $0.00
 |  |  |  | $0.00 |  | $0.00
 |  |  |  | $0.00 |  | $0.00
 |  |  |  | $0.00 |  | $0.00
 |  |  |  | $0.00 |  | $0.00
 |  |  |  | $0.00 |  | $0.00
 |  |  |  | $0.00 |  | $0.00
 |  |  |  | $0.00 |  | $0.00
 |  |  |  | $0.00 |  | $0.00
 |  |  |  | $0.00 |  | $0.00
 |  |  |  | $0.00 |  | $0.00

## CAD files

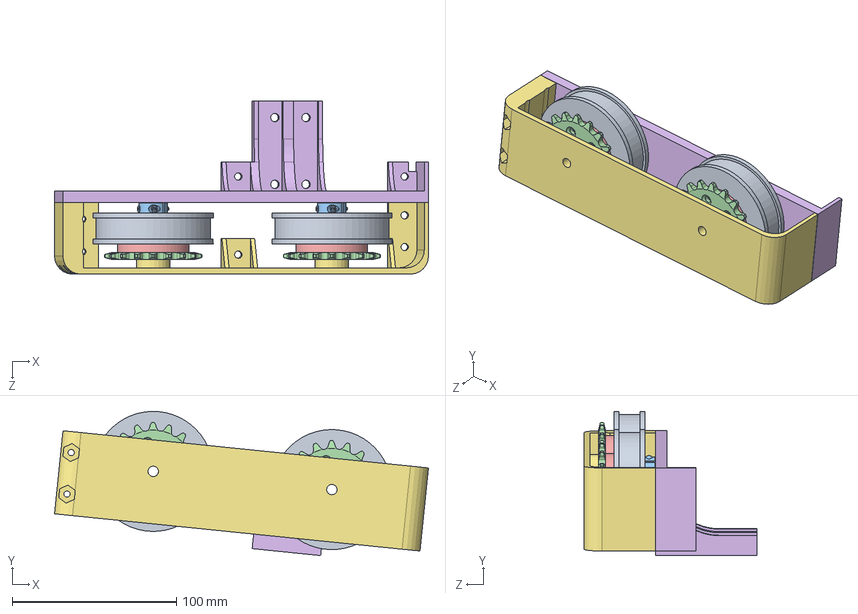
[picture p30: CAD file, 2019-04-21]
Mechanical-Hardware/CAD/wheelTotalRight2.SLDASM
227.5 x 87.7 x 105.4 mm
wheel x 2
6383K213_BALL BEARING x 4
6436K131_TWO-PIECE CLAMP-ON SHAFT COLLAR x 4
2299K307_MACHINABLE-BORE FLAT SPROCKET x 2
Copy of Part6 x 2
outerBorder
bumperRight

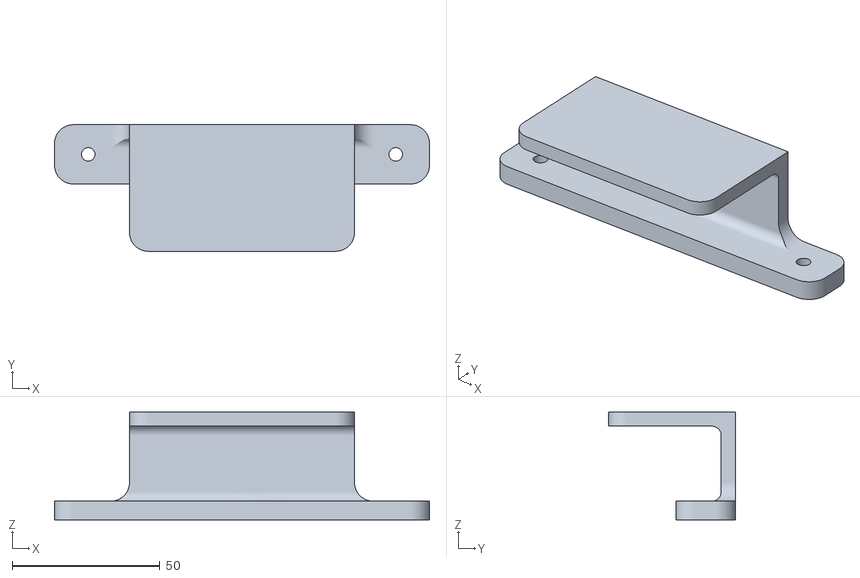
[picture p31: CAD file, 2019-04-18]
Mechanical-Hardware/3D-Prints/orange/main_batt_bracket_V2.STL
127.0 x 42.9 x 36.5

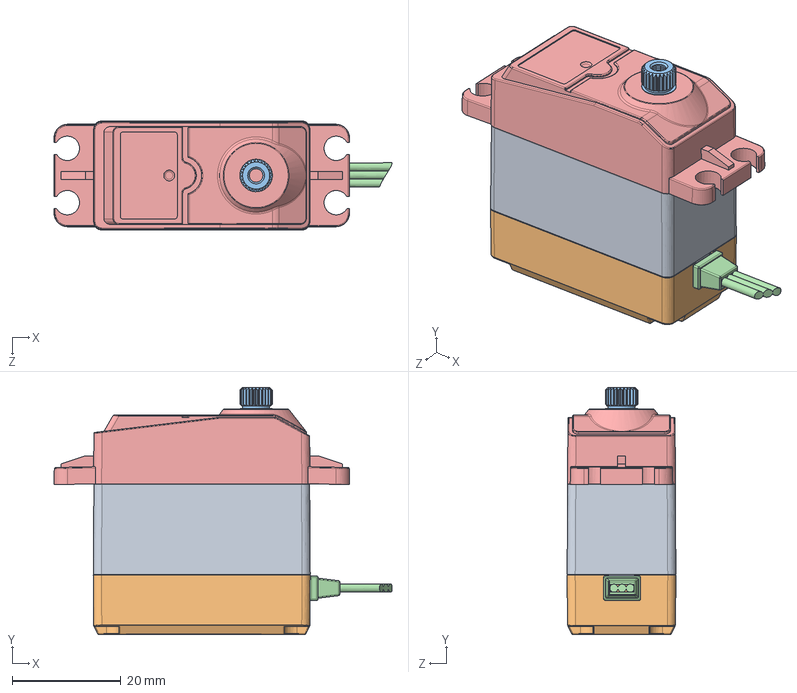
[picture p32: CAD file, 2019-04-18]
Mechanical-Hardware/CAD/DS3218.SLDASM
62.2 x 45.5 x 20.0 mm
ZK
DG-SZ
GE
XIANTAO
SG-JIANRONG-MG996

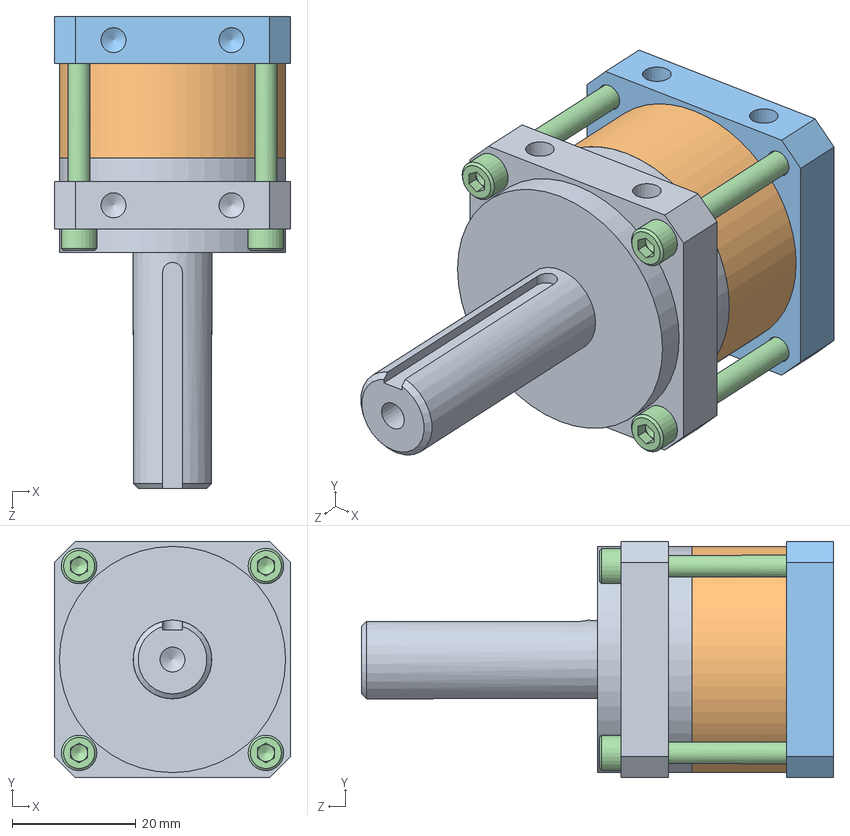
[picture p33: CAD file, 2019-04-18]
Mechanical-Hardware/CAD/am-2875+Banebots+P60+4-1.SLDASM
38.1 x 38.1 x 76.2 mm
P60 shaft plate and shaft
P60 1-stage ring gear
P60 motor plate
socket head cap screw_ai_HX-SHCS 0.138-32x1.25x0.75-N x 4

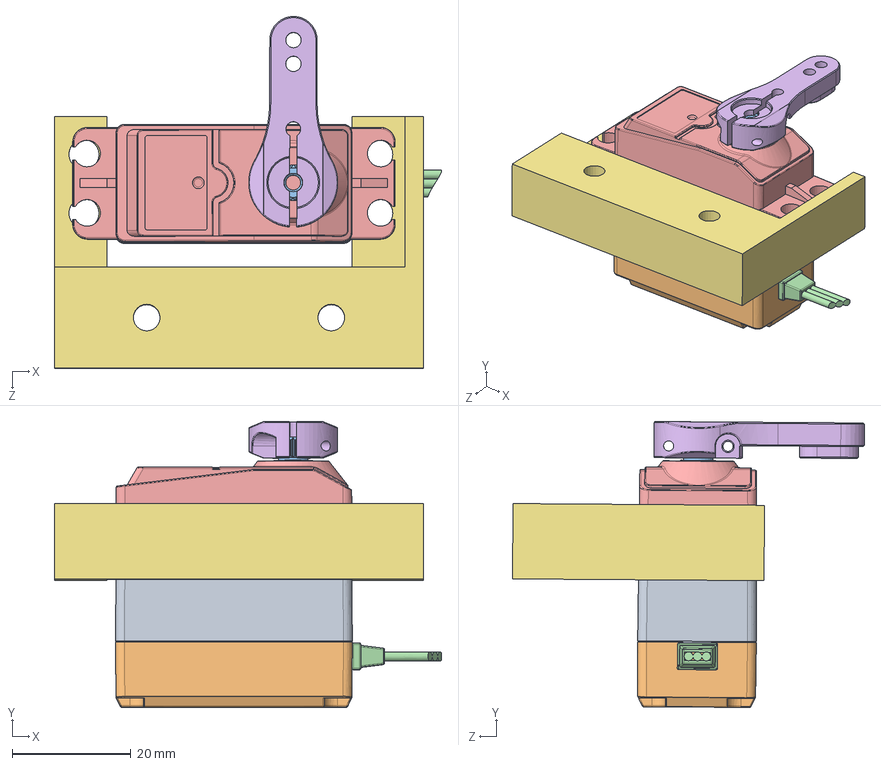
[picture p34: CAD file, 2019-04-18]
Mechanical-Hardware/CAD/servoAssembly.SLDASM
65.3 x 48.2 x 59.3 mm
ZK
DG-SZ
GE
XIANTAO
SG-JIANRONG-MG996
LV-DUOBAN
servoMount

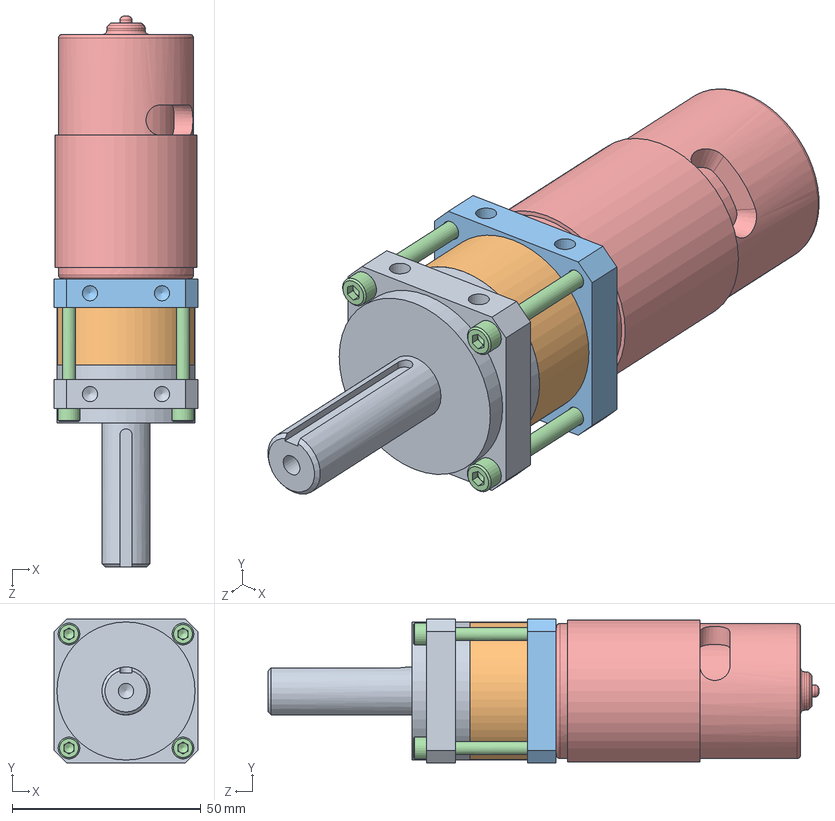
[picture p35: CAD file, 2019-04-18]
Mechanical-Hardware/CAD/555Gearbox16P60.SLDASM
38.1 x 38.1 x 145.7 mm
P60 shaft plate and shaft
P60 1-stage ring gear
P60 motor plate
socket head cap screw_ai_HX-SHCS 0.138-32x1.25x0.75-N x 4
Mabuchi 555

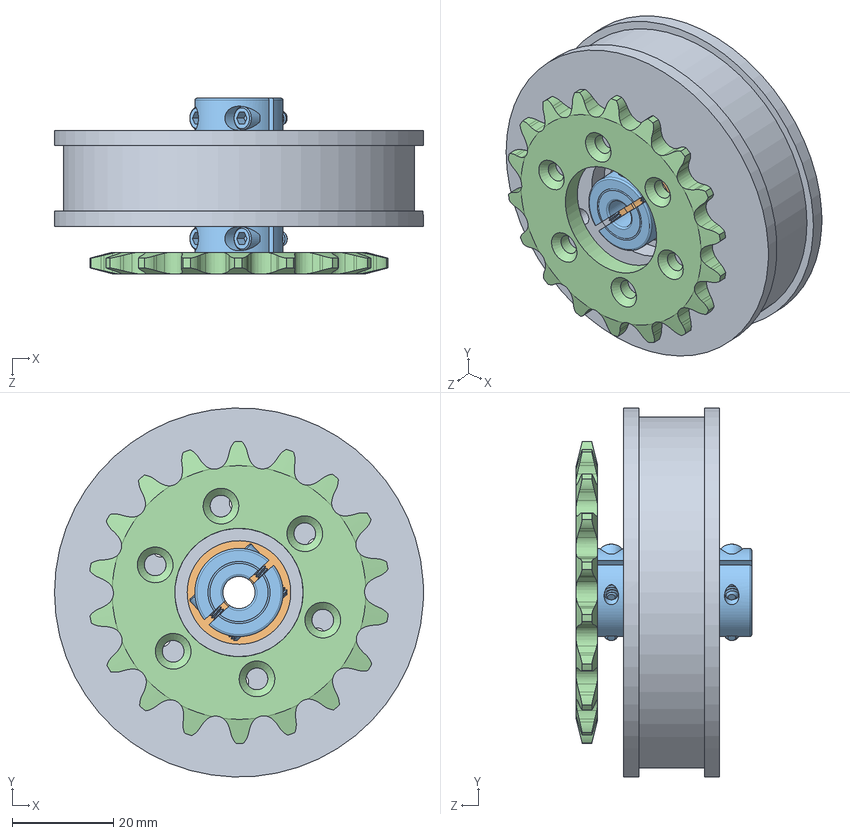
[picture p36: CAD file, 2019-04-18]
Mechanical-Hardware/CAD/WheelAssembly2.SLDASM
73.0 x 73.0 x 34.8 mm
wheel
6383K213_BALL BEARING x 2
6436K131_TWO-PIECE CLAMP-ON SHAFT COLLAR x 2
2299K307_MACHINABLE-BORE FLAT SPROCKET

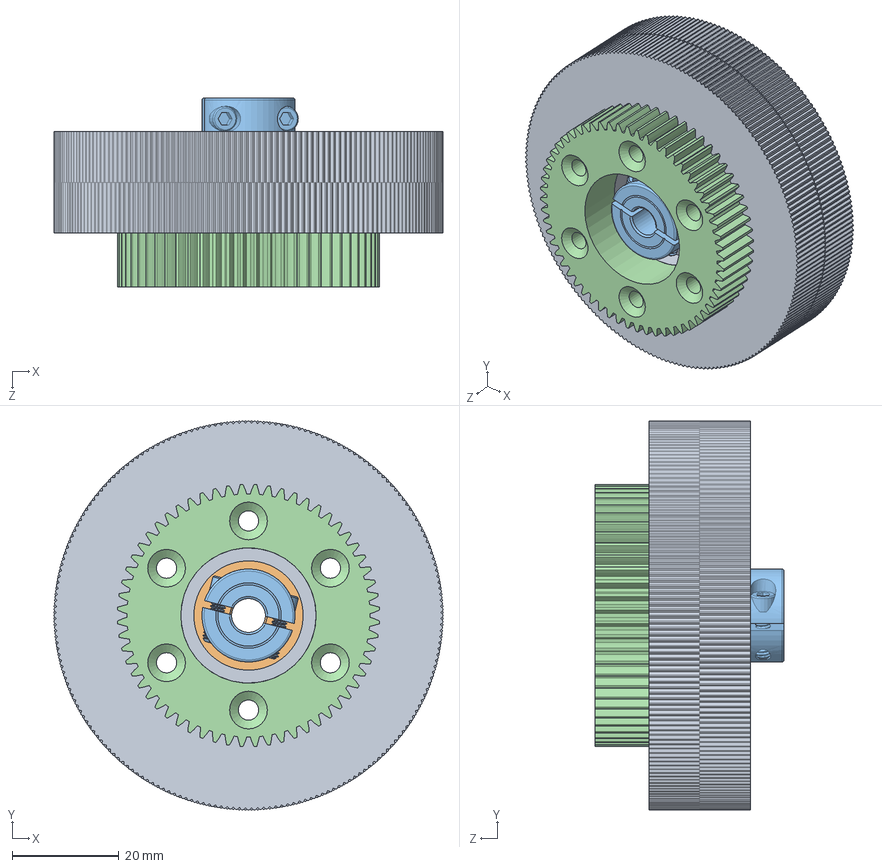
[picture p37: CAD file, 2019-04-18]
Mechanical-Hardware/CAD/WheelAssembly.SLDASM
73.0 x 73.0 x 35.6 mm
wheel
6383K213_BALL BEARING x 2
6436K131_TWO-PIECE CLAMP-ON SHAFT COLLAR x 2
spur gear_ai2

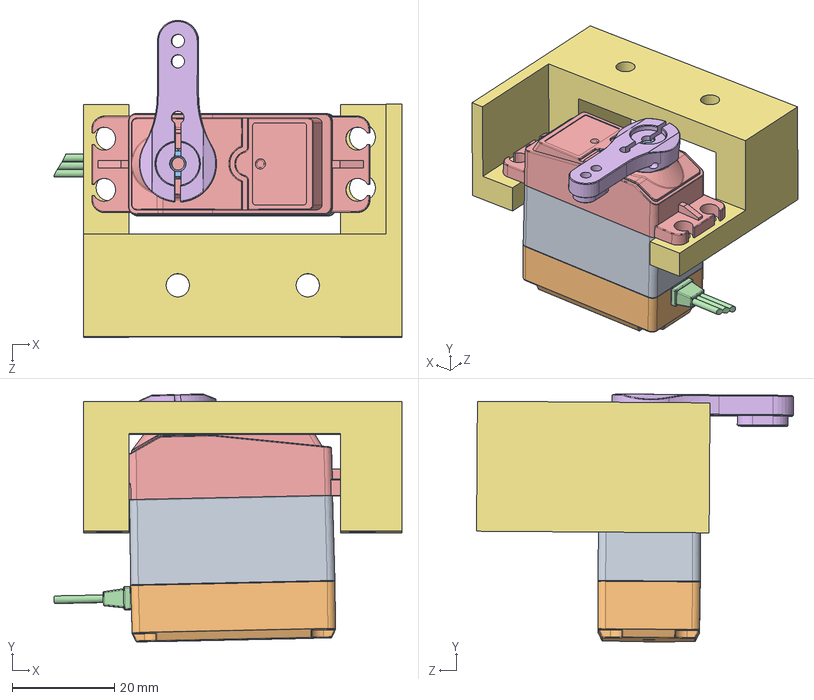
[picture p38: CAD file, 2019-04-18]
Mechanical-Hardware/CAD/servoAssembly2.SLDASM
68.0 x 48.5 x 62.0 mm
ZK
DG-SZ
GE
XIANTAO
SG-JIANRONG-MG996
LV-DUOBAN
servoMount2

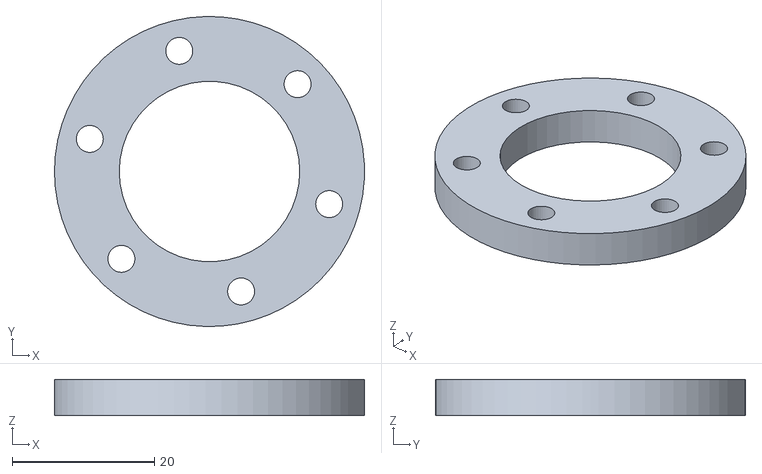
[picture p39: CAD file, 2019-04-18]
Mechanical-Hardware/3D-Prints/blue/4xWheelSpacer.STL
43.7 x 43.6 x 5.08

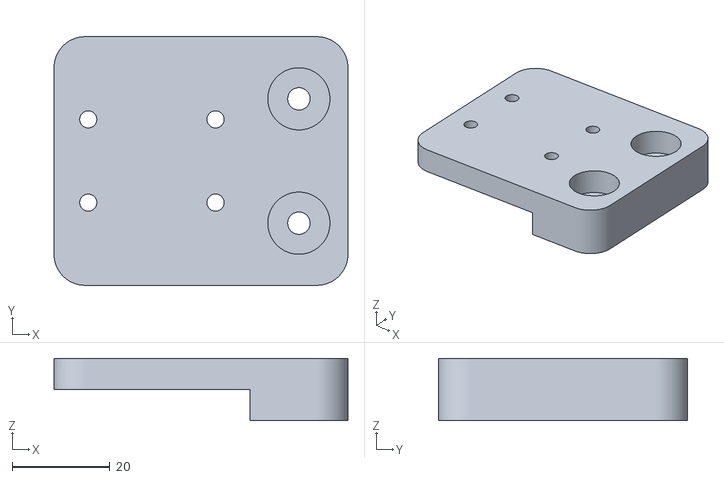
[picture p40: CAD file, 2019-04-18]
Mechanical-Hardware/3D-Prints/orange/lidarController_Mount.STL
60.1 x 50.8 x 12.7

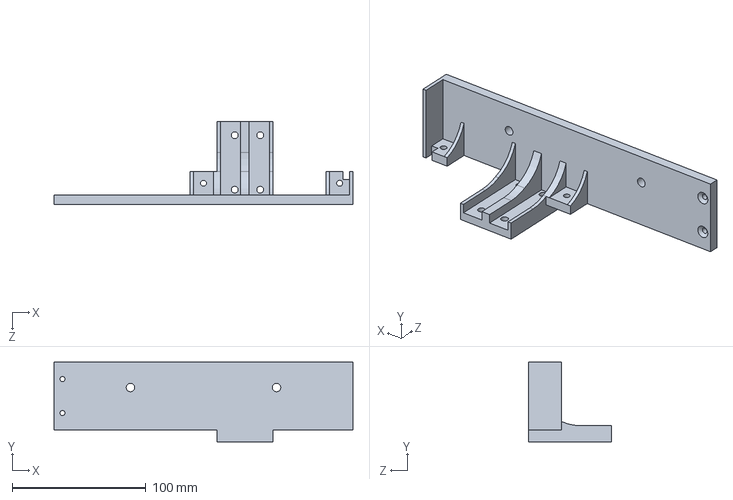
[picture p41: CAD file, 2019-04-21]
Mechanical-Hardware/CAD/outerBorder.SLDPRT
223.5 x 59.7 x 61.8 mm

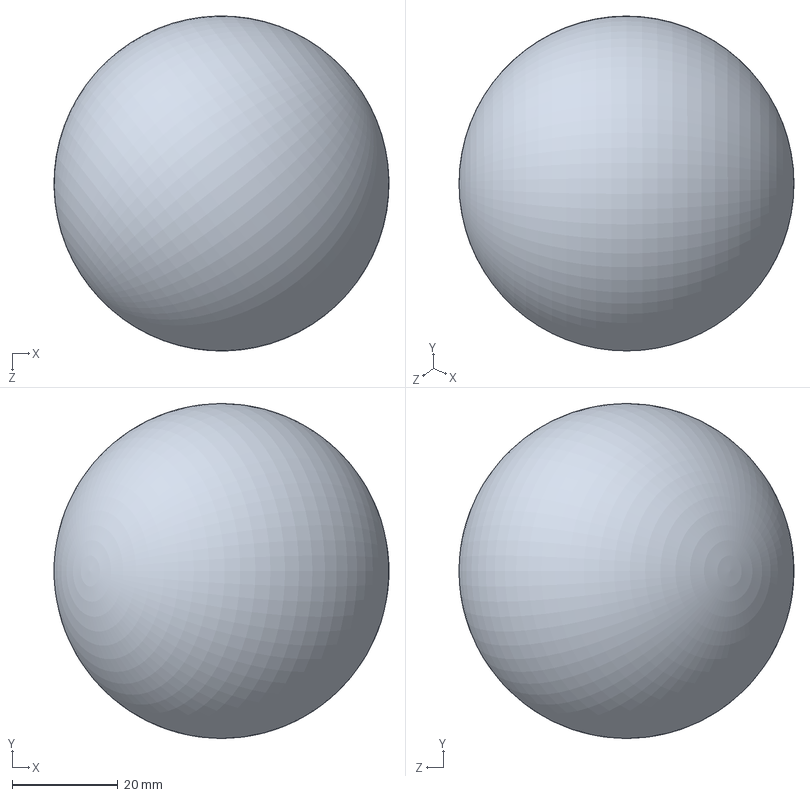
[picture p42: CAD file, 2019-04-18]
Mechanical-Hardware/FieldElements/Sphere.SLDPRT
63.5 x 63.5 x 63.5 mm

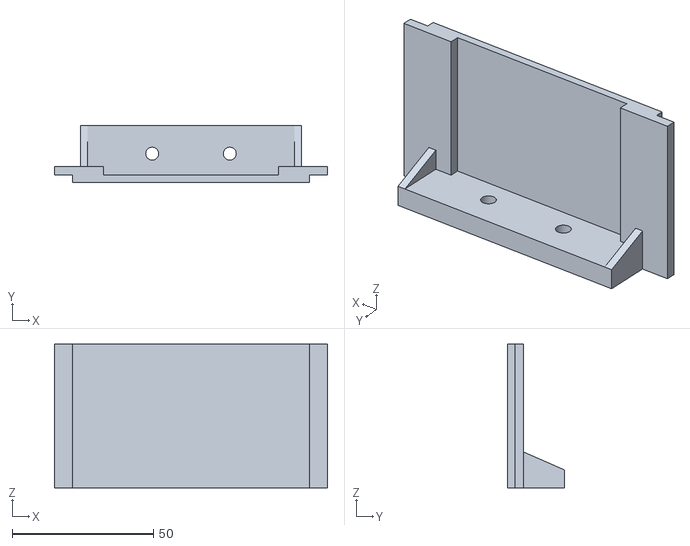
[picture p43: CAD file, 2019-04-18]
Mechanical-Hardware/3D-Prints/blue/bumperBack.STL
96.5 x 20.1 x 50.8

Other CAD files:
Mechanical-Hardware/CAD/wheelTotalLeft2.SLDASM
Mechanical-Hardware/CAD/main_batt_bracket_V2.SLDPRT
Mechanical-Hardware/3D-Prints/orange/lidarMount_V2.STL
Mechanical-Hardware/FieldElements/Cube.SLDPRT
Mechanical-Hardware/3D-Prints/blue/2XencoderBracket.STL
Mechanical-Hardware/3D-Prints/blue/2xgear1.STL
Mechanical-Hardware/3D-Prints/blue/2xgear2.STL
Mechanical-Hardware/3D-Prints/blue/4xSprocket.STL
Mechanical-Hardware/3D-Prints/blue/ElectronicsBase.STL
Mechanical-Hardware/3D-Prints/blue/FlagServoMount.STL
Mechanical-Hardware/3D-Prints/blue/Pi-2nd-Holder.STL
Mechanical-Hardware/3D-Prints/blue/leftInner.STL
Mechanical-Hardware/3D-Prints/blue/leftOuter.STL
Mechanical-Hardware/3D-Prints/blue/rightInner.STL
Mechanical-Hardware/3D-Prints/blue/rightOuter.STL
Mechanical-Hardware/3D-Prints/blue/teensyBracket.STL
Mechanical-Hardware/3D-Prints/orange/4xWheel.STL
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

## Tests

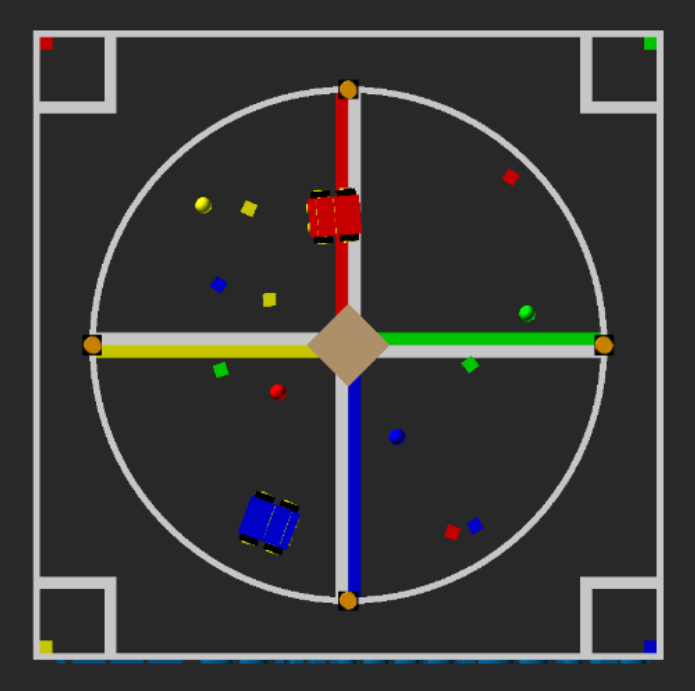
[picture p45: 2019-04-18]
Images/Field Testing/Capture.PNG

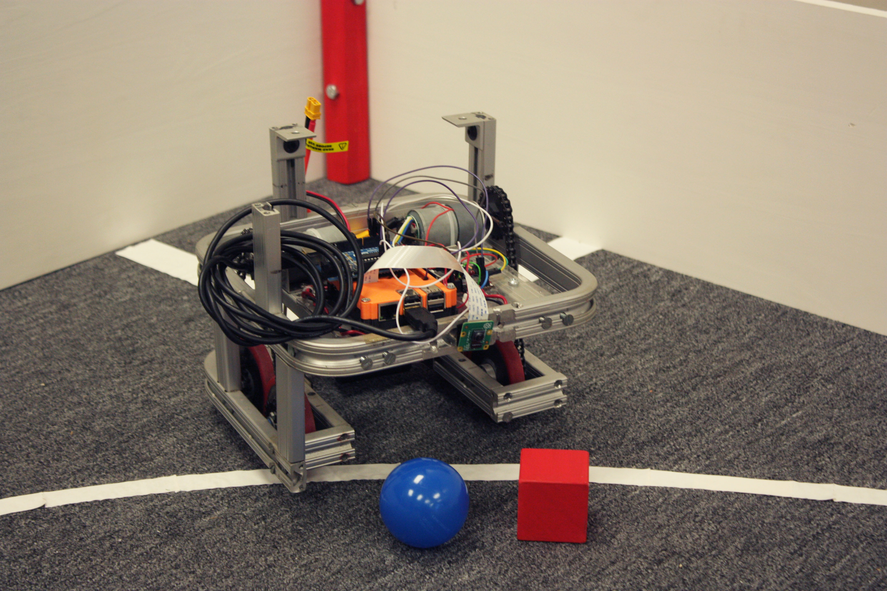
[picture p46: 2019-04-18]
Images/Field Testing/test-bot.JPG

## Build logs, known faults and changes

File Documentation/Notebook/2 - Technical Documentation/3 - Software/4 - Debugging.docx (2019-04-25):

Debugging (04/25/19)

The following guide is representative of the system as of the date above. Methods are subject to change as the system changes.

“I can’t connect to either Pi”

- Plug each one in manually to a computer monitor and check that they are connected to the same network you are
- Attempt to ping the Pis via their addresses on your network. This can be checked by using ifconfig

“RViz, RQT, etc.. can’t connect to my Pi / I can’t see any data”

- Most of the time this happens when one Pi is not connected via WiFi to your network.
- You’ll find that the nodes run on that Pi will not be seen in the RQT graph.

“My robot won’t localize itself after moving”

- This is an in-depth problem, as there can be many sources of error. AMCL is what allows the robot to determine where it is in the global space. It uses primarily the laser scan data and the odometry (encoders). Ensure both are outputting what you would expect with rostopic echo
- Ensure you define the correct initial position in the amcl_diff.launch file. Don’t forget the orientation (in radians)

“The robot won’t go to the correct spot I defined”

- Ensure the position you defined is within the map space using RViz.
- There are currently several bugs with the navigation stack to be worked out. Using the move_base nodes that use costmaps seem to have the most trouble with navigation

Known Bugs (04/25/19)

- Move_Base node is still sporadic and a primary cause of being unable to navigate the space
- The /pid_velocity nodes are currently untuned, so they have been changed to a static range of 20%-50% in motor power terms. (The robot overcomes the power of inertia at 20%) This should be fixed at some point to allow the robot to be more accurate
- AMCL sometimes will lose its position if it does not move for an extended period

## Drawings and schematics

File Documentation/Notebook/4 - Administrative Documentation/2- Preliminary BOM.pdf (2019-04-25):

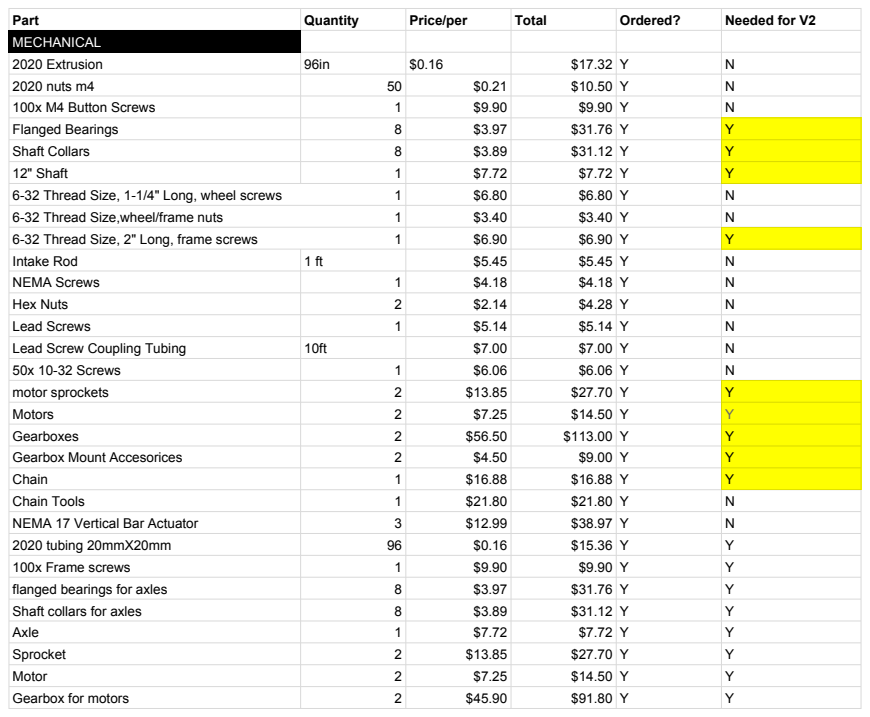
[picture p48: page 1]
Part; Quantity; Price/per; Total; Ordered?; Needed for V2; MECHANICAL; 2020 Extrusion; 2020 nuts m4; 100x M4 Button Screws; Intake Rod; NEMA Screws; Hex Nuts; Lead Screws; Lead Screw Coupling Tubing; 50x 10-32 Screws; motor sprockets; Motors; Gearboxes; Gearbox Mount Accesorices; Chain; Chain Tools; NEMA 17 Vertical Bar Actuator; 2020 tubing 20mmX20mm; 100x Frame screws; flanged bearings for axles; Shaft collars for axles; Axle; Sprocket; Motor; Gearbox for motors

Flanged Bearings 8 $3.97 $31.76 Y Shaft Collars 8 $3.89 $31.12 Y 12" Shaft 1 $7.72 $7.72 Y | Y Y Y

6-32 Thread Size, 1-1/4" Long, wheel screws 6-32 Thread Size,wheel/frame nuts 6-32 Thread Size, 2" Long, frame screws | 1 $6.80 $6.80 Y N 1 $3.40 $3.40 Y N

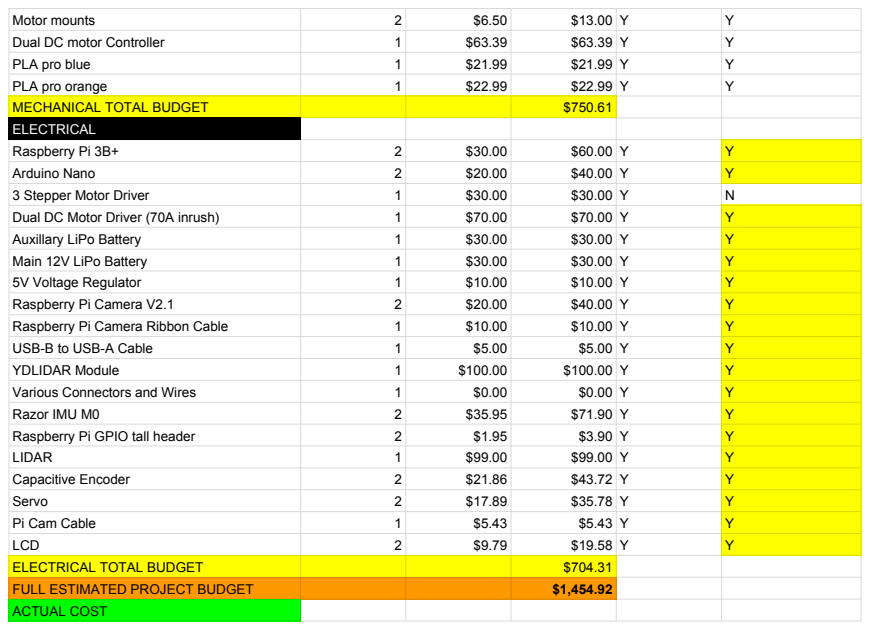
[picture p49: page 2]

Motor mounts
Dual DC motor Controller
PLA pro blue
PLA pro orange

MECHANICAL TOTAL BUDGET $750.61
ELECTRICAL

Raspberry Pi 3B+
Arduino Nano
3 Stepper Motor Driver
Dual DC Motor Driver (70A inrush)
Auxillary LiPo Battery
Main 12V LiPo Battery
5V Voltage Regulator
Raspberry Pi Camera V2.1
Raspberry Pi Camera Ribbon Cable
USB-B to USB-A Cable
YDLIDAR Module
Various Connectors and Wires
Razor IMU M0
Raspberry Pi GPIO tall header
LIDAR
Capacitive Encoder
Servo
Pi Cam Cable
LCD

ELECTRICAL TOTAL BUDGET $704.31
FULL ESTIMATED PROJECT BUDGET $1,454.92
ACTUAL COST

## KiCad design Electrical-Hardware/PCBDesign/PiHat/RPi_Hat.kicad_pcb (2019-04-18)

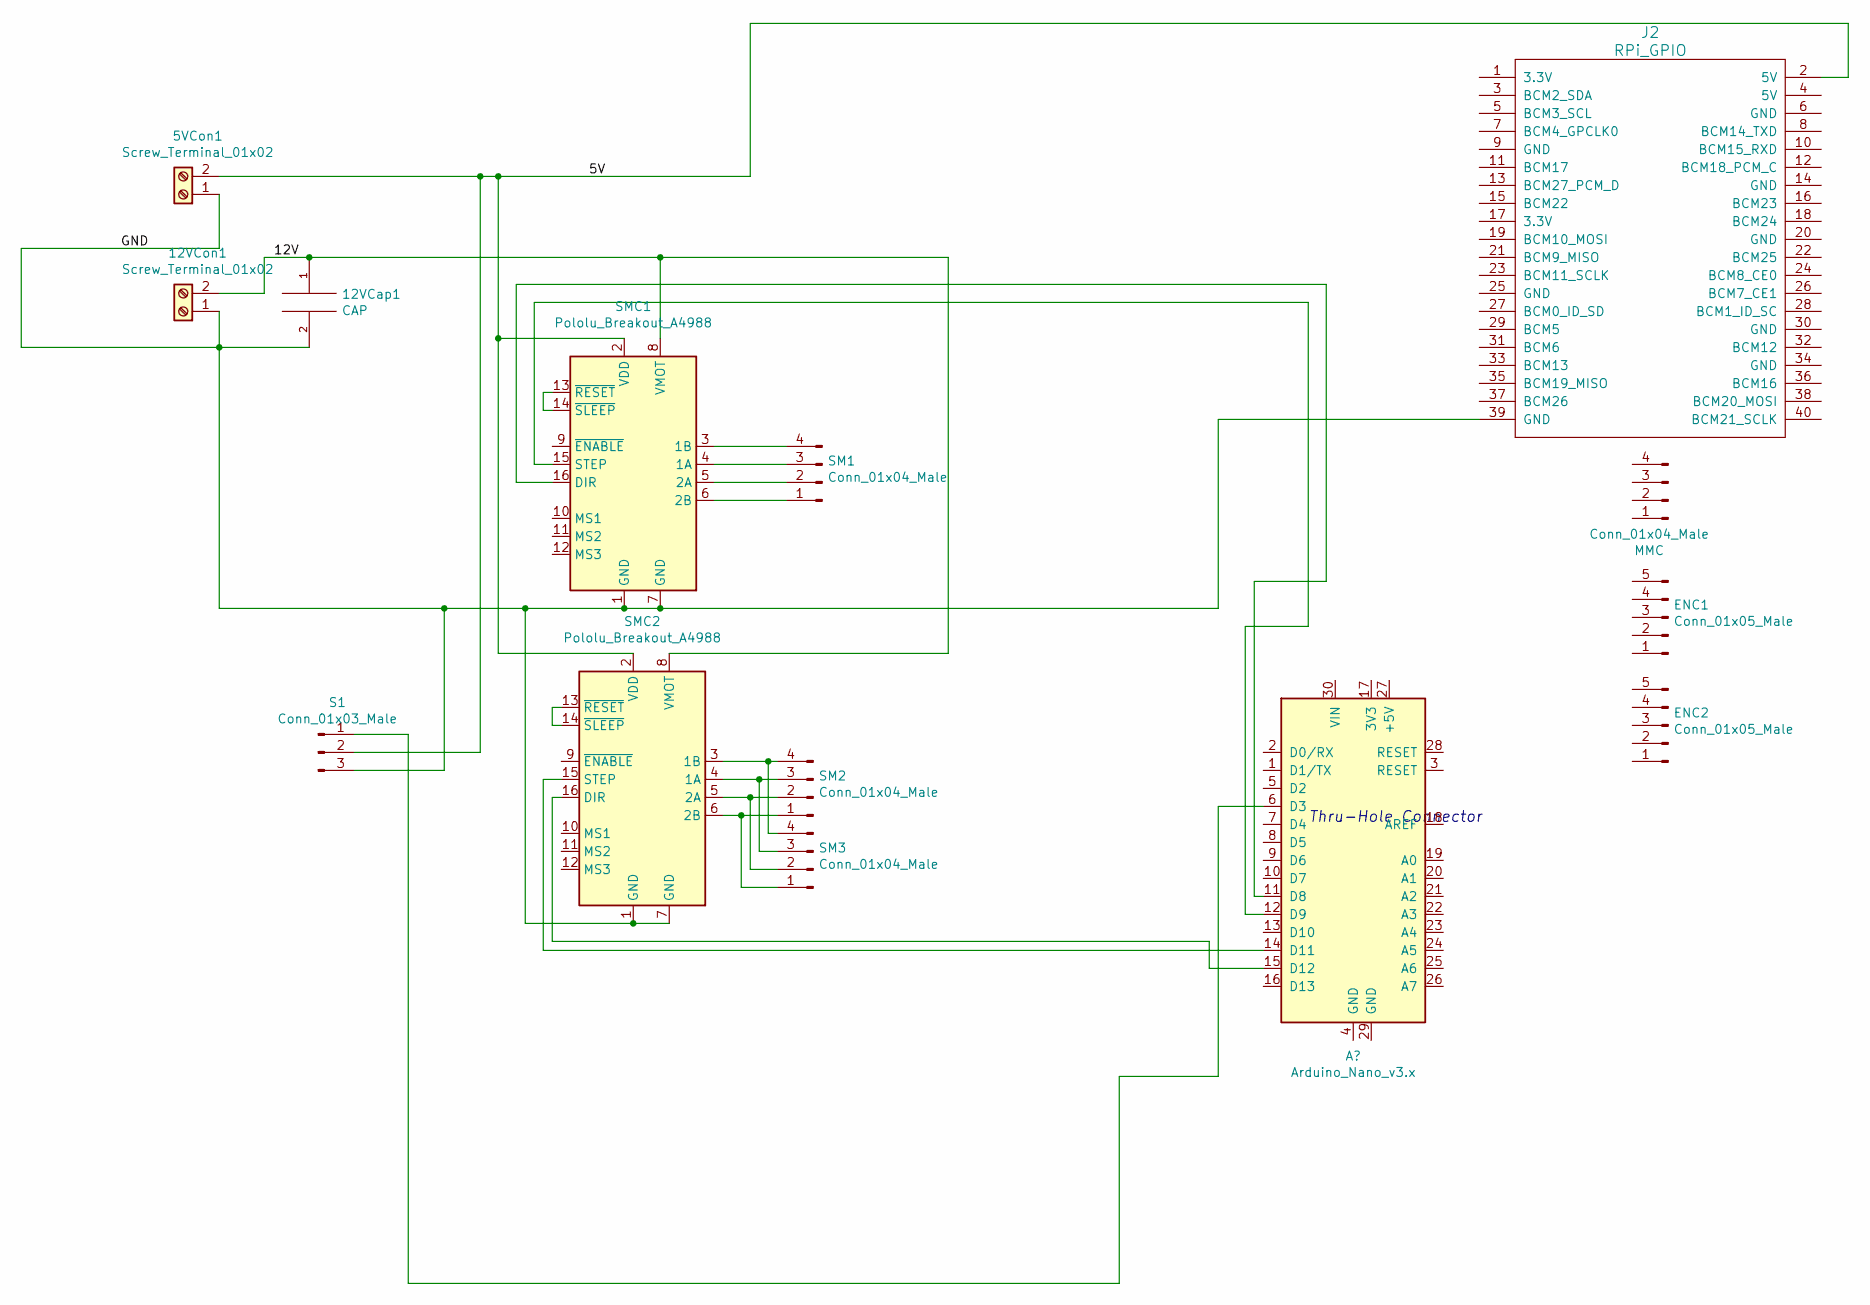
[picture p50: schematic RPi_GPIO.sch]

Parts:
5VCon1, 12VCon1: Screw_Terminal_01x02; TerminalBlock_bornier-2_P5.08mm
12VCap1: CAP; C_Rect_L9.0mm_W6.7mm_P7.50mm_MKT
ENC1, ENC2: Conn_01x05_Male; PinHeader_1x05_P2.54mm_Vertical
J2: RPi_GPIO; Pin_Header_Straight_2x20
MMC: Conn_01x04_Male; NS-Tech_Grove_1x04_P2mm_Vertical
S1: Conn_01x03_Male; PinHeader_1x03_P2.54mm_Vertical
SM1, SM2, SM3: Conn_01x04_Male; PinHeader_1x04_P2.54mm_Vertical
SMC1, SMC2: Pololu_Breakout_A4988; Pololu_Breakout-16_15.2x20.3mm

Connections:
/RPi_GPIO/5V: 5VCon1.2, J2.2 (5V), S1.2, SMC1.2 (VDD), SMC2.2 (VDD)
/RPi_GPIO/12V: 12VCap1.1, 12VCon1.2, SMC1.8 (VMOT), SMC2.8 (VMOT)
/RPi_GPIO/GND: 5VCon1.1, 12VCap1.2, 12VCon1.1, J2.39 (GND), S1.3, SMC1.1 (GND), SMC1.7 (GND), SMC2.1 (GND), SMC2.7 (GND)
unnamed 8: S1.1; also elsewhere on the board
unnamed 13: SMC1.16 (DIR); also elsewhere on the board
unnamed 14: SMC1.15 (STEP); also elsewhere on the board
unnamed 16: SMC2.15 (STEP); also elsewhere on the board
unnamed 17: SMC2.16 (DIR); also elsewhere on the board
unnamed: SM1.1, SMC1.6 (2B)
unnamed: SM1.2, SMC1.5 (2A)
unnamed: SM1.3, SMC1.4 (1A)
unnamed: SM1.4, SMC1.3 (1B)
unnamed: SM2.1, SM3.1, SMC2.6 (2B)
unnamed: SM2.2, SM3.2, SMC2.5 (2A)
unnamed: SM2.3, SM3.3, SMC2.4 (1A)
unnamed: SM2.4, SM3.4, SMC2.3 (1B)
unnamed: SMC1.13 (~RESET), SMC1.14 (~SLEEP)
unnamed: SMC2.13 (~RESET), SMC2.14 (~SLEEP)

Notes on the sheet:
Thru-Hole Connector

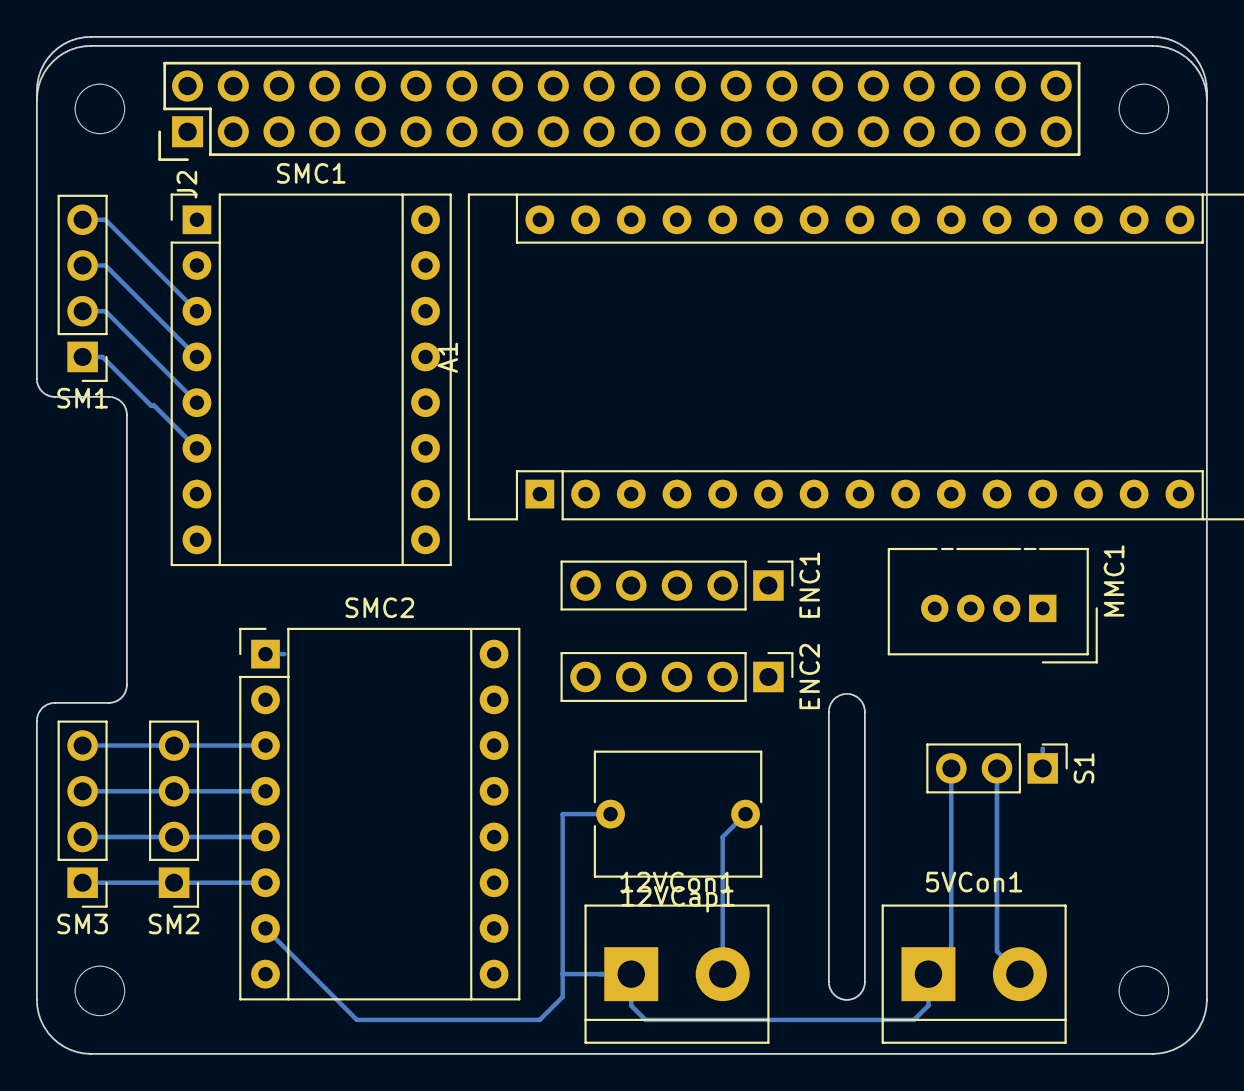
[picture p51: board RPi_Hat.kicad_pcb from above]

Board: 2 copper layers, 65.0 x 56.5 mm, 14 parts (0 on the bottom side), 18 nets.

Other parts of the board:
A1: Arduino_Nano_v3.x; Arduino_Nano
MMC1: Conn_01x04_Male; NS-Tech_Grove_1x04_P2mm_Vertical

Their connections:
unnamed 8: A1.6; also elsewhere on the board
unnamed 13: A1.11; also elsewhere on the board
unnamed 14: A1.12; also elsewhere on the board
unnamed 16: A1.14; also elsewhere on the board
unnamed 17: A1.15; also elsewhere on the board

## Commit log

2019-04-18 Uploaded files from gitlab. Git history cannot transfer due to file size.
    [2020-8in.SLDPRT, 2299K307_MACHINABLE-BORE FLAT SPROCKET.SLDPRT, 2XencoderBracket.STL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]
2019-04-21 fixed CAD, added pictures, updated diagrams, and updated poster
    [Copy of Part1.sldprt, bumperBack.SLDPRT, encoderBracket.SLDPRT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]
2019-04-23 updated poster, added edited Josh's pictures, added PO's
    [PO_01-14-19_IEEE.xlsx, PO_01-24-19_IEEE.xlsx, PO_02-05-19_IEEE.xlsx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]
2019-04-25 Preparing documentation for notebook
    [PO_01-14-19_IEEE.xlsx, PO_01-24-19_IEEE.xlsx, PO_02-05-19_IEEE.xlsx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]
